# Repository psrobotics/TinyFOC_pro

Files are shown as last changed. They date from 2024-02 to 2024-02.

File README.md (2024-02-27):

# TinyFOC_pro

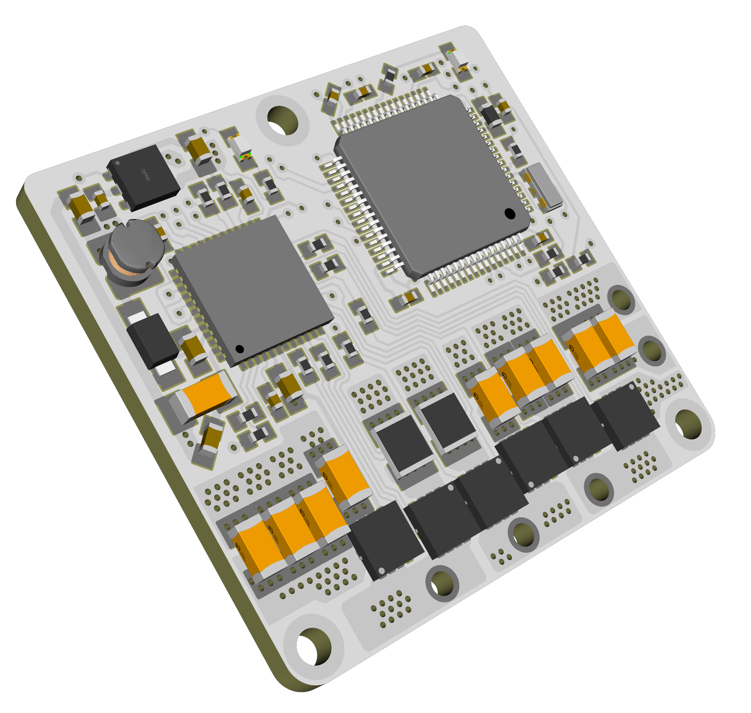
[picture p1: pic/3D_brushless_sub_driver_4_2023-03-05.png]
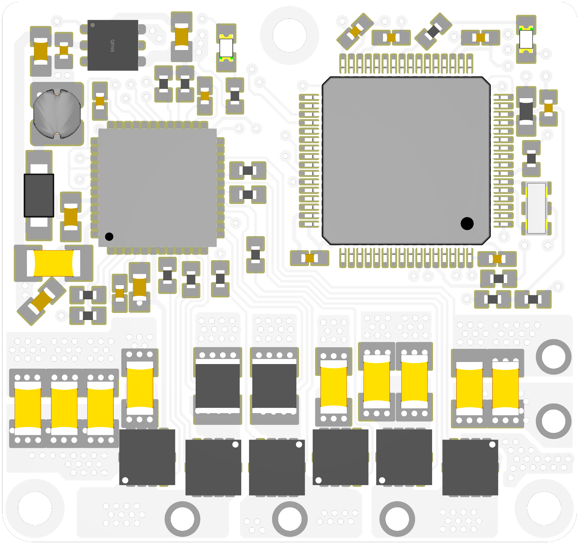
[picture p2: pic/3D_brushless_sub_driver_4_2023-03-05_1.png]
<br><br>
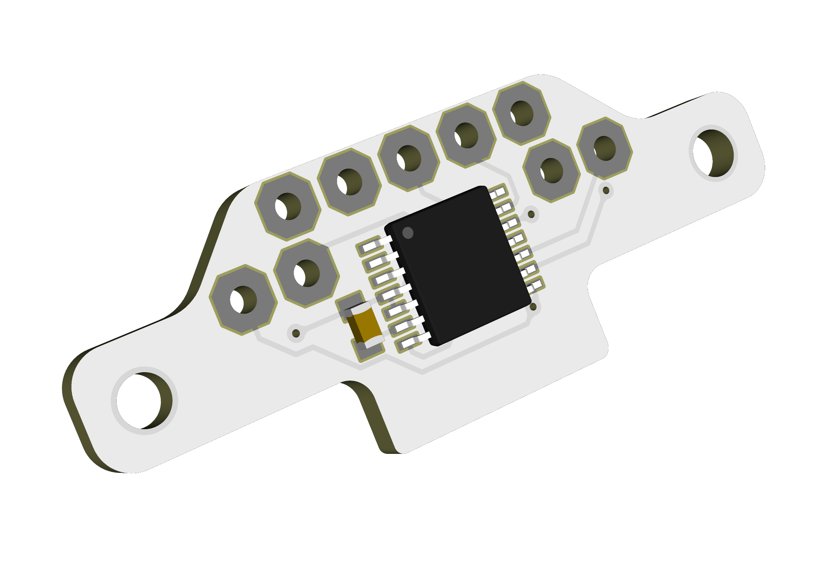
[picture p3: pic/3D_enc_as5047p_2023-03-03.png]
<br>
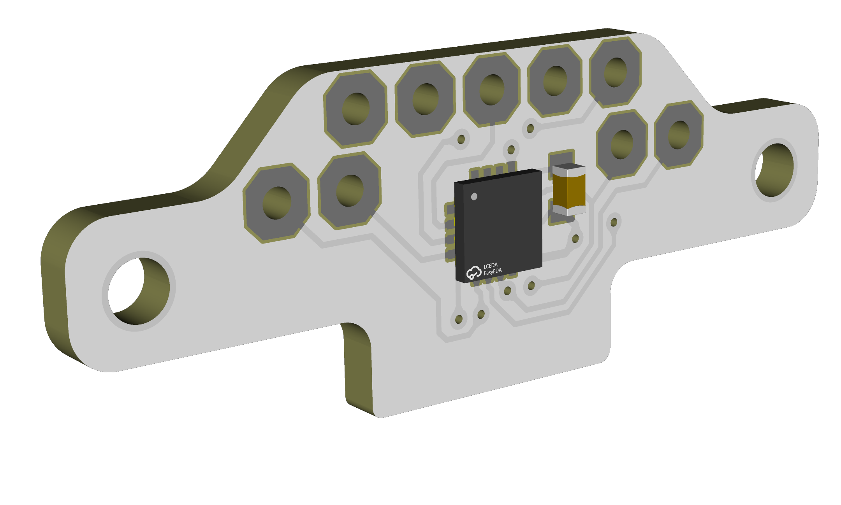
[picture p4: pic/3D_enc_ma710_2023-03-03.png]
<br>

<br><br>

* Compact brushless motor driver modified from [mit mini cheetah driver](https://github.com/bgkatz/3phase_integrated)
* 12 bit GMR-based encoder with MA710 or AS5047p
* CAN, hardware serial

Design file exported with [Autodesk EAGLE](https://www.autodesk.com/products/eagle/overview?term=1-YEAR&tab=subscription)

## License
MIT License

## Contact
* Shuang Peng, {shuangpe}@usc.edu

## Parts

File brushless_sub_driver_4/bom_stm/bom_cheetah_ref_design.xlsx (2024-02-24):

Supplied Parts
Qty Per Board | Value | Device | Package | Parts | MFG Part | 57
1 | DRV8323RH | DRV8323RH | QFN50P700X700X90-49N | U$1 | ‎DRV8323RSRGZT‎
2 | G | LED0603 | LED-0603 | LED1, LED2 | LTST-C191KRKT‎
1 | 3.3V 500 mA LDO | LDFM | DFN6-3X3 | LDFM33PUR | ‎LDFM33PUR‎
1 | MA700 | MA700 | QFN16 | U$11 | ‎MA700GQ-Z‎
1 | MCP2542 | MCP2542 | TDFN | U$6 | ‎MCP2542FDT-H/MNY‎
1 | SM07B-SRSS-TB | SM07B-SRSS-TB | SM07B-SRSS-TB | PROG | ‎SM07B-SRSS-TB(LF)(SN)‎
1 | STM32F446RET6 | STM32F446RET6 | TQFP64 | U$3 | ‎STM32F446RET6‎
6 | 60V | MOSFET | Power SO8 | Q1, Q2, Q3, Q4, Q5, Q6 | ‎TPH2R506PL,L1Q‎
9 | 10 uF 50v | C-USC1206K | C1206K | C1, C8, C11, C12, C13, C14, C15, C16, C17, C21, C22, C23, C24, C25, C26, C28, C29 | GRT31CR61H106ME01L
1 | 22uH 500 mA | SDR0302 | SDR0302 | L1 | ‎NRH3012T220MN‎
2 | 0.001 | R-US_R1210 | R1210 | R6, R7 | ‎PMR25HZPFV1L00‎
1 | 600r | INDUCTOR0603 | 603 | CHOKE | ‎PE-0603FB601ST‎
1 | 8 Mhz Ceramic Resonator | CSTCE | CSTCE | XT1 | ‎CSTNE8M00GH5L000R0‎
1 | 500 mA 60v | DIODE-SOD123 | SOD123 | D1 | ‎MBR0580S1-7‎
8 | .1 uF 10v X5R/X7R | C-USC0402K | C0402K | C18, C27, C31, C32, C33, C34, C41, VREFCAP | ‎CL05A104MP5NNNC
2 | .1 uF 50v X5R/X7R | C-USC0603K | C0603K | C2, C4 | ‎CC0603JRX7R9BB104‎
3 | 1 uF 10v X5R/X7R | C-USC0402K | C0402K | C7, C10, MC1 | ‎CL05A105MP5NNNC‎
1 | 1 uF 50v X5R/X7R | C-USC0603K | C0603K | C6 | ‎CL10A105KB8NNNC‎
4 | 10k 1% | R-US_R0402 | R0402 | R2, R3, R4 R27 | ‎RT0402DRE0710KL‎
1 | 150k 1% | R-US_R0402 | R0402 | R26 | ‎RMCF0402FT150K‎
2 | 200 5% | R-US_R0402 | R0402 | R5, R22 | ‎RC0402JR-07200RL‎
3 | 22 uF 10v X5R/X7R | C-USC0603K | C0603K | C3, C19, C20 | ‎CL10A226MPCNUBE‎
1 | 4.7 uF 10v X5R/X7R | C-USC0402K | C0402K | C9 | ‎GRM155R60J475ME87D‎
1 | 47 nF 50v X5R/X7R | C-USC0402K | C0402K | C5 | ‎CGA2B3X7R1H473M050BD‎
1 | 54.9k 1% | R-US_R0402 | R0402 | R1 | ‎RC0402FR-0754K9L‎
1 | 3-Pin |  | SM03B-SRSS-TB | SER1 | SM03B-SRSS-TB

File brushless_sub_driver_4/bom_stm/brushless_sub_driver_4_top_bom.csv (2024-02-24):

Comment | Designator | Footprint | LCSC Part #
.001 | R8 R9 | R1210
0.1uF | C2 C4 | C0603K
0.1uF | C17 | C1206K
1 uF | C6 | C0603K
1uF | C7 C10 | C0402K
1uF | C22 | C0402
2.2 | R6 R7 R10 R11 R12 R13 | R0402
3.3uH | CHOKE | 0603
4.7k | R14 R15 | R0402
4.7uF | C9 | C0402K
10k | R2 R3 R4 R27 | R0402
10uF | C1 C8 C11 C12 C13 C14 C15 C16 C18 | C1206K
22 uF | C3 | C0603K
22uF | C25 | C0603K
22uH | L1 | SDR0302
47 nF | C5 | C0402K
54.9k | R1 | R0402
100nF | C27 C31 C32 | C0402K
100nF | C41 | C0402
100nF | VREFCAP | C0402K
150k | R26 | R0402
200 | R5 R22 | R0402
AON7544 | Q7 Q8 Q9 Q10 Q11 Q12 | AON7544
CSTCE | XT1 | CSTCE
DRV8323RH | DRV1 | QFN50P700X700X90-49N
LD39050PUR | U3 | SON95P300X300X100-7N
SOD123 | D1 | SOD123
STM32F446RET6 | U1 | TQFP64
green | D2 D3 | 0603P

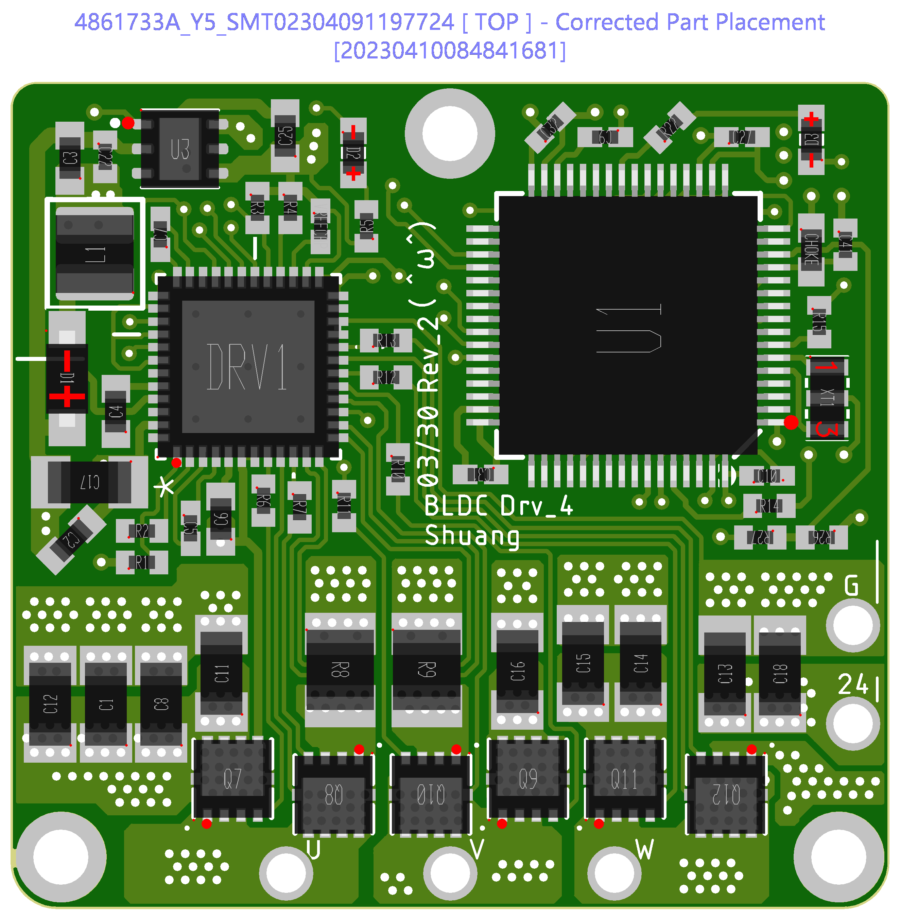
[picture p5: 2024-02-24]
brushless_sub_driver_4/bom_stm/Produce_SMT_FINAL_Snapshot_top_0410.png

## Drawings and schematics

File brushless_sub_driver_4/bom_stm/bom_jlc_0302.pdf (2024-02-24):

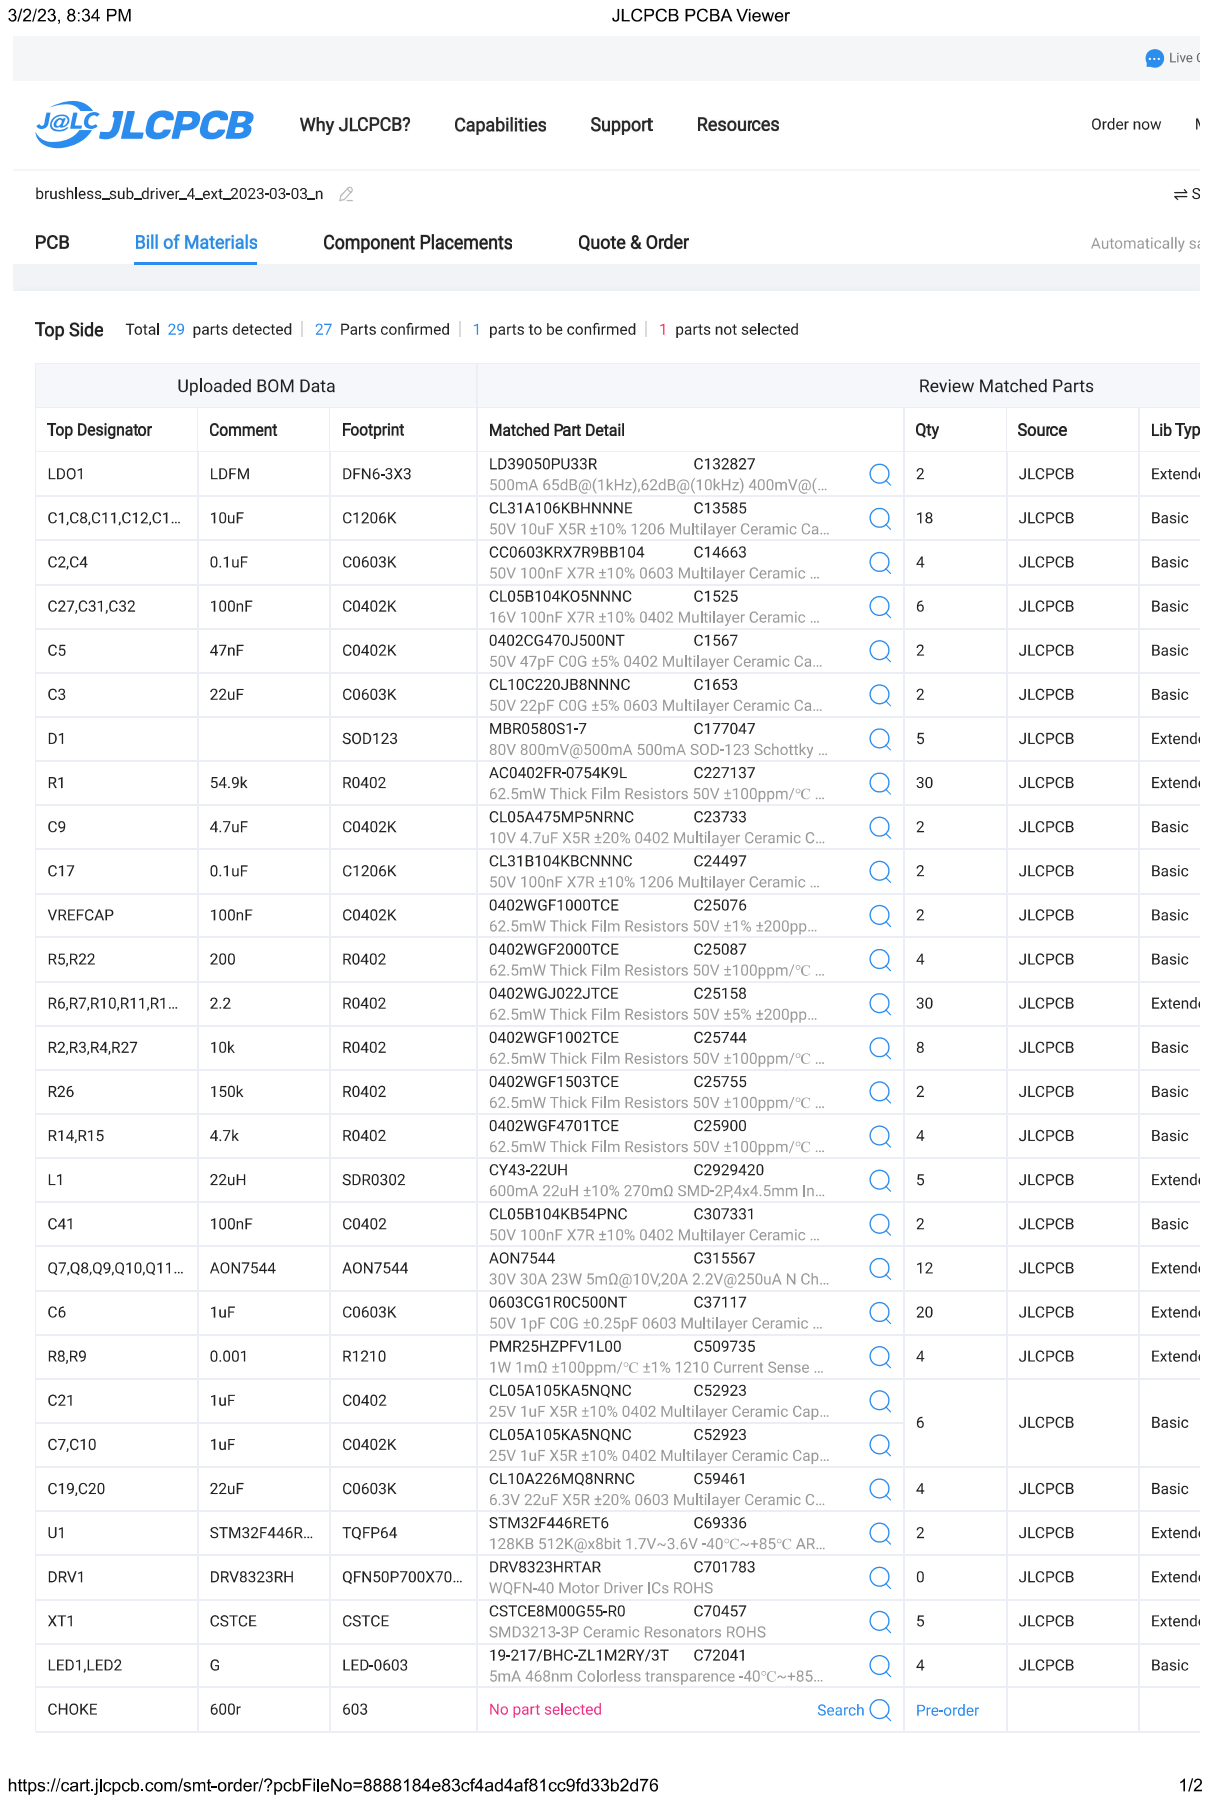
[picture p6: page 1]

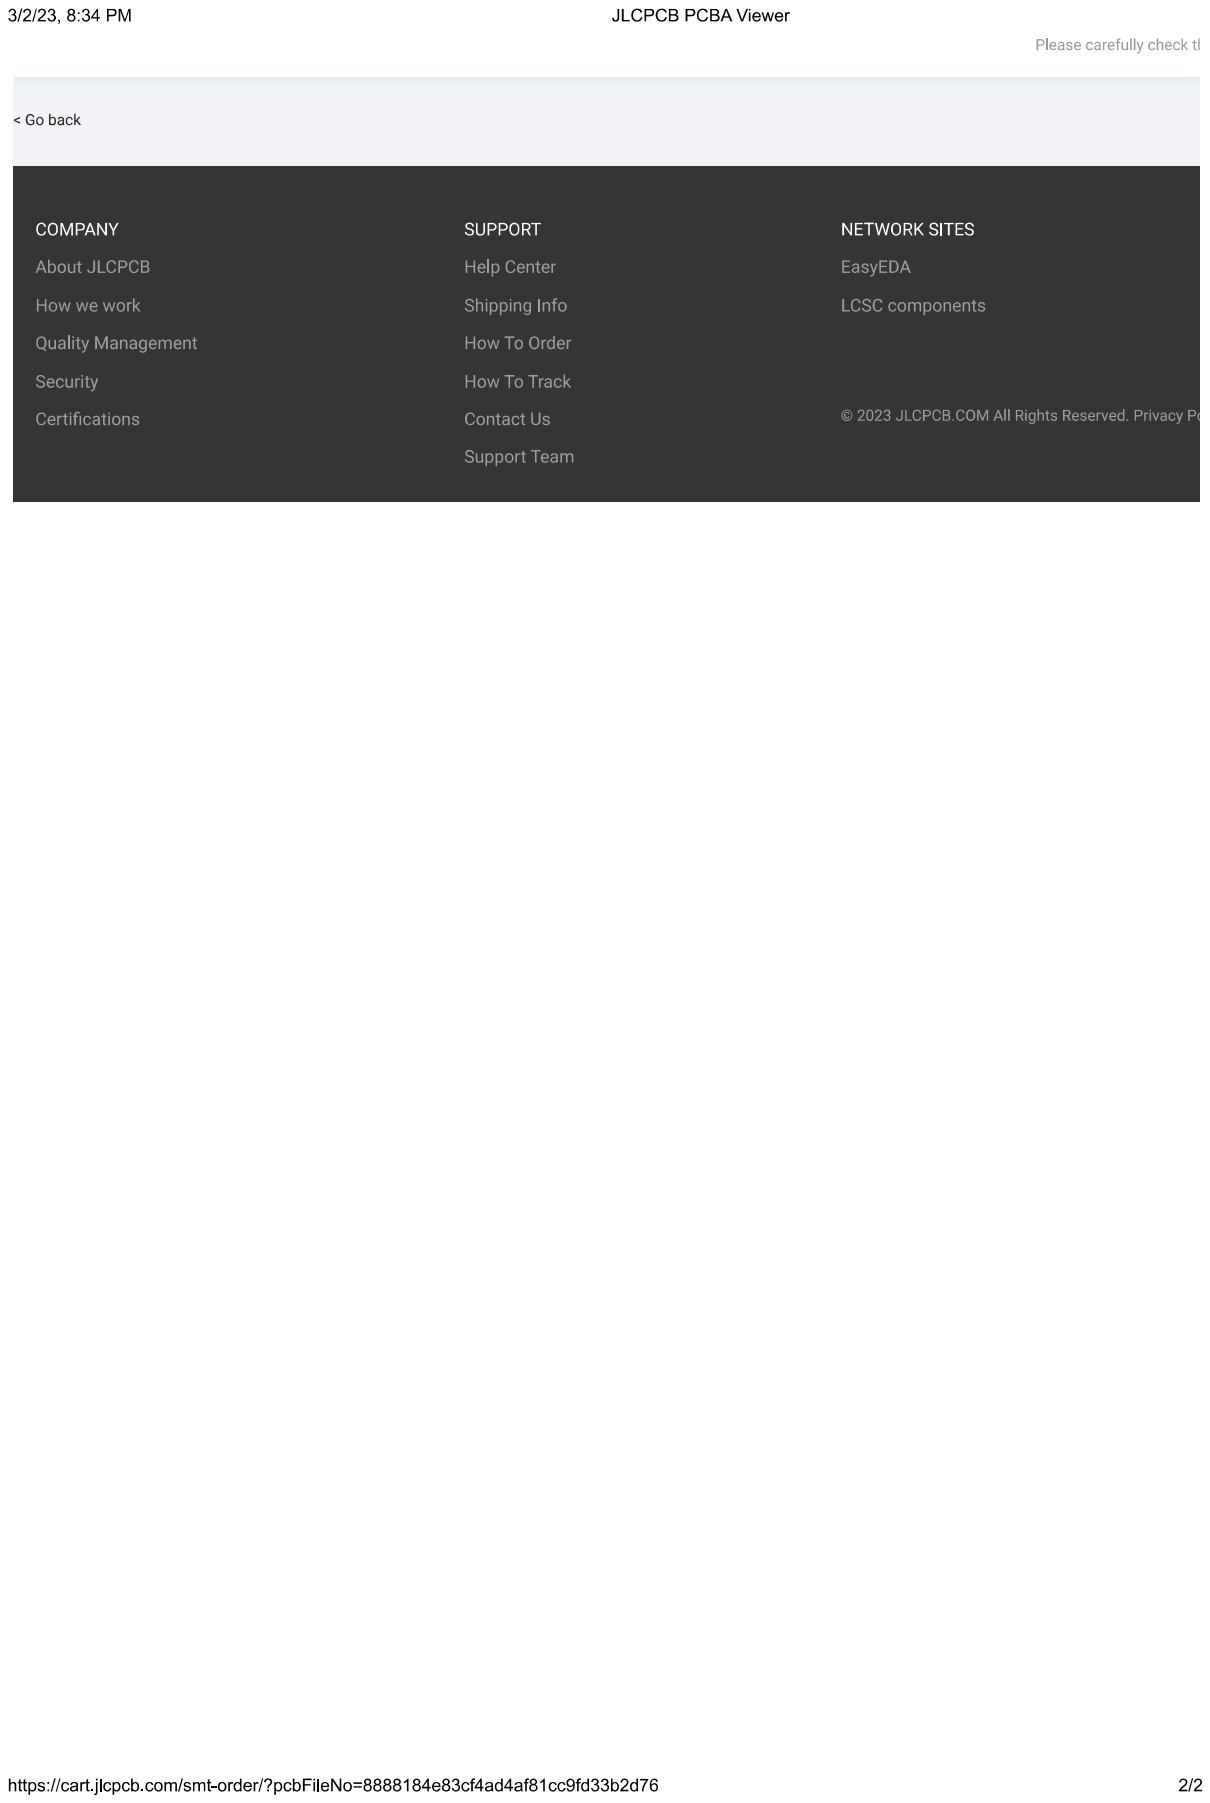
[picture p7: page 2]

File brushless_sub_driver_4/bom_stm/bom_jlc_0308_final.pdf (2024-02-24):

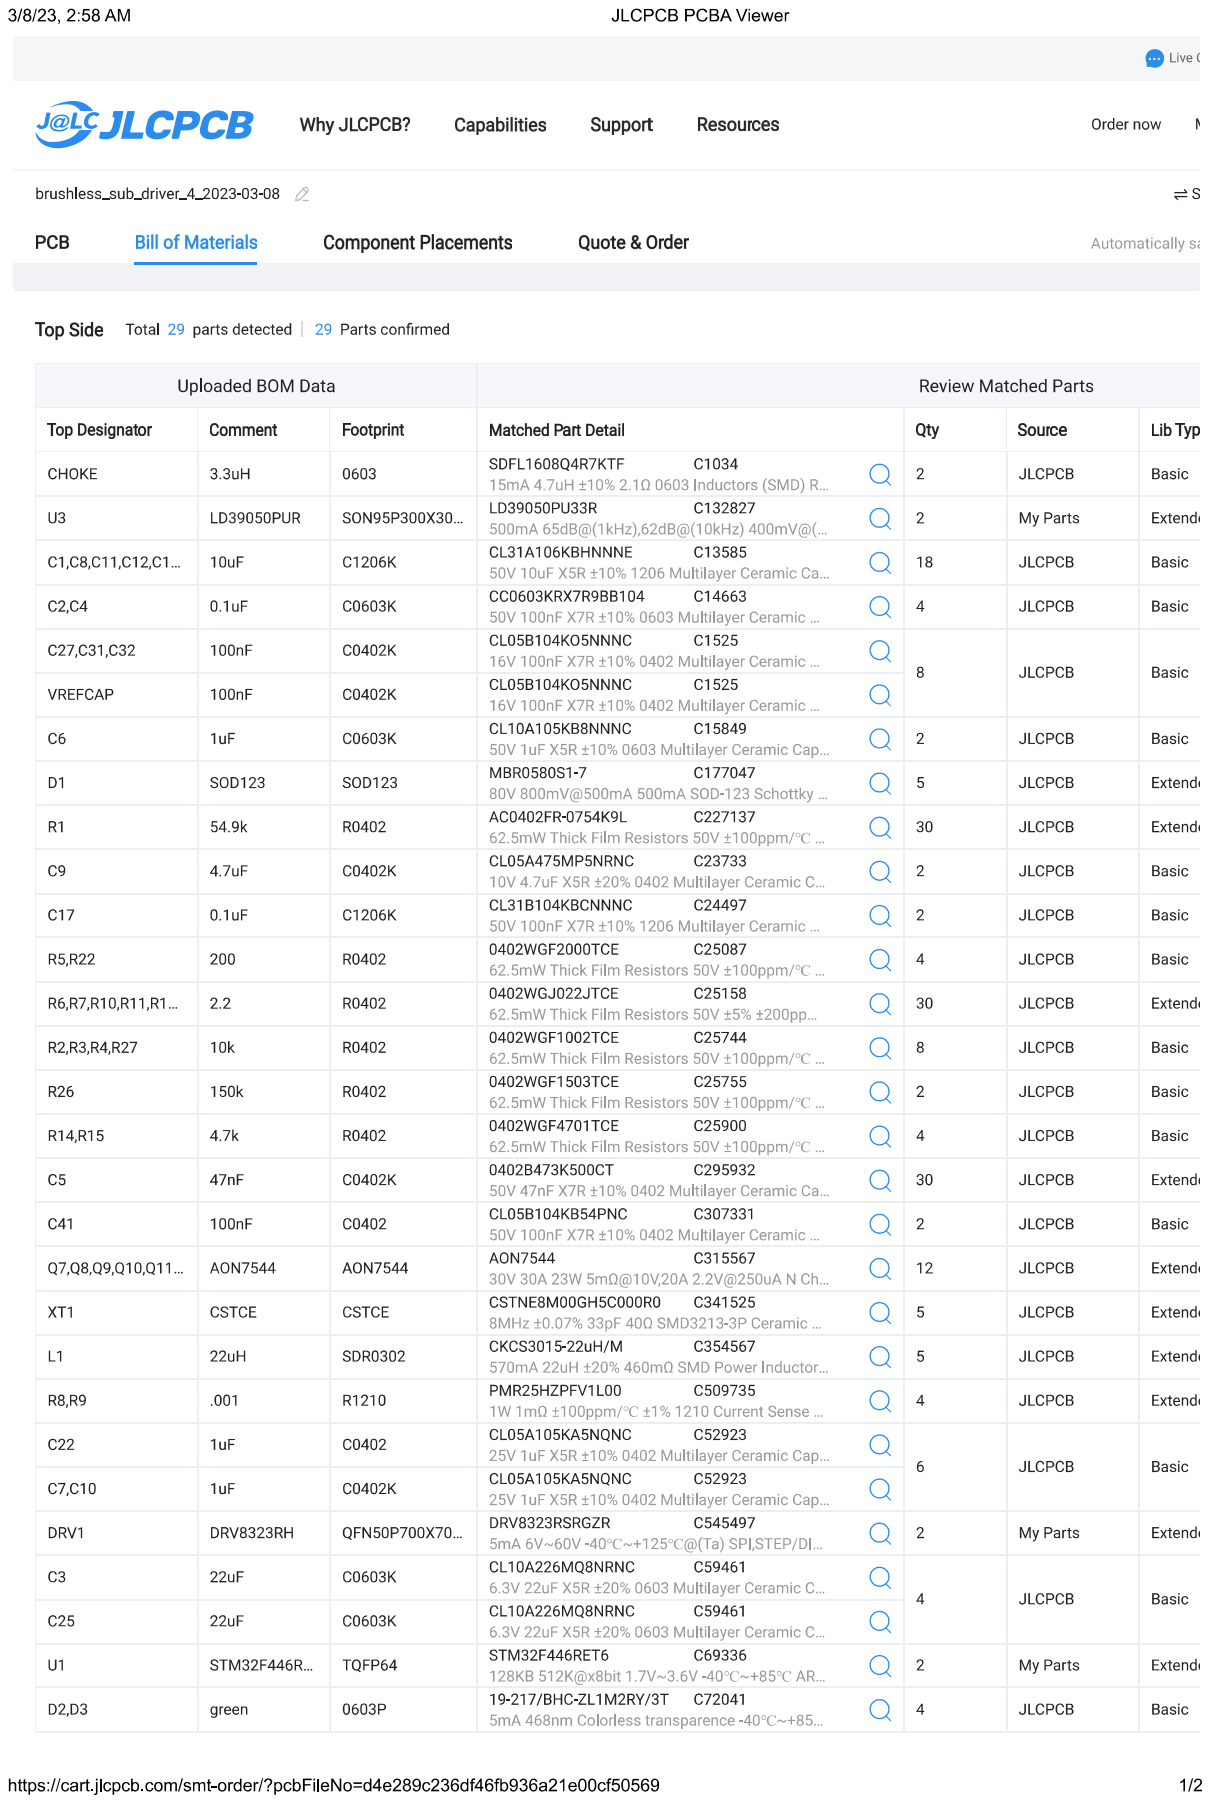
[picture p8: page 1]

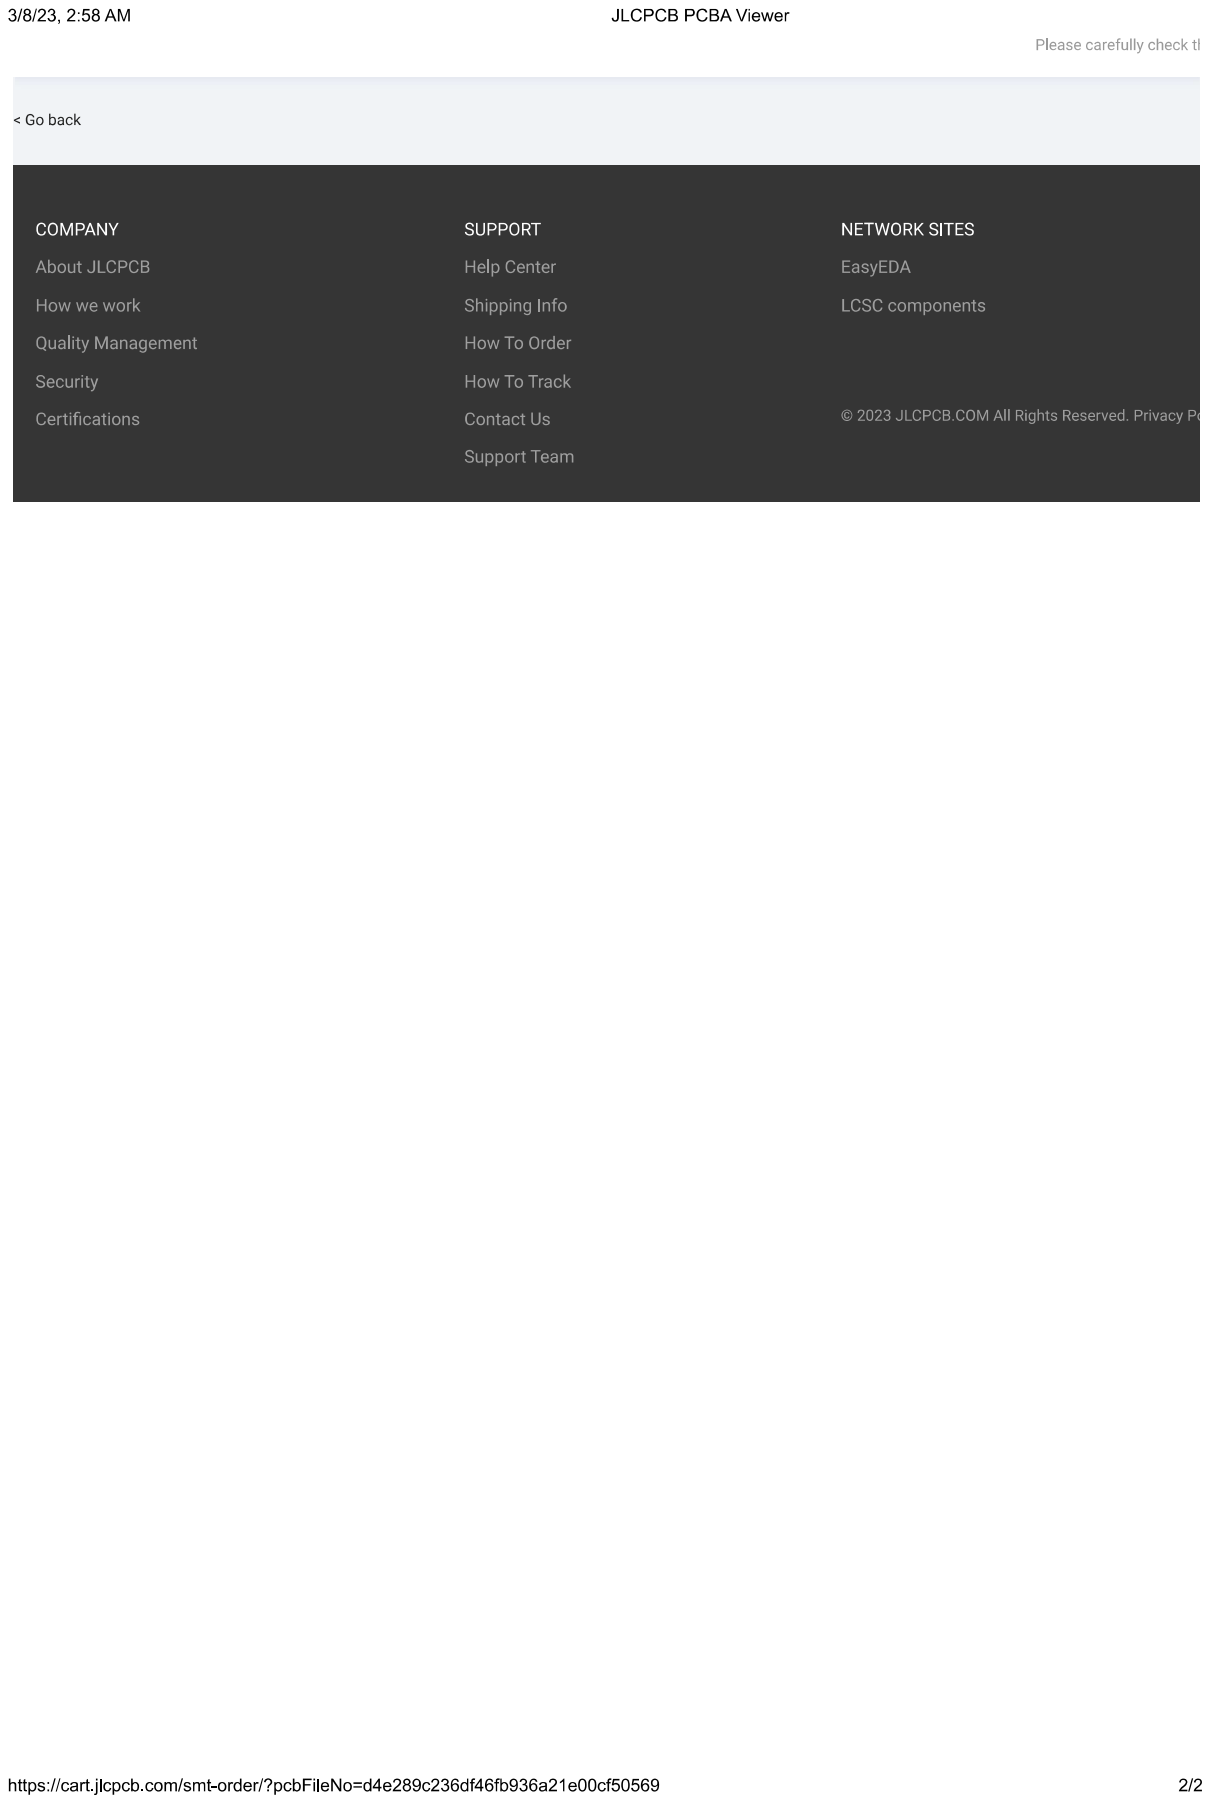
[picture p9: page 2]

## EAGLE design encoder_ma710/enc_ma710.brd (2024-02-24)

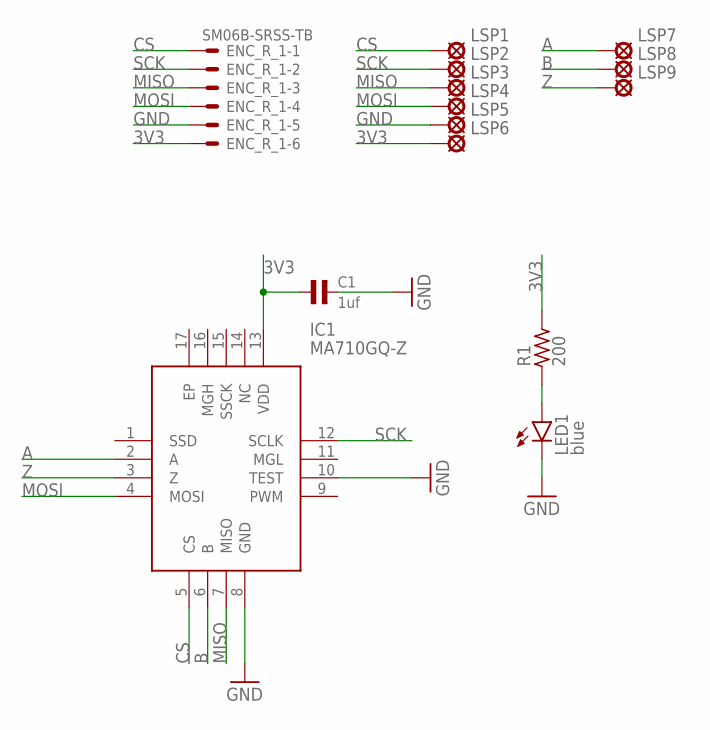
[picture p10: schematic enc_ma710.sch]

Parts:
C1: 1uf; 0603
ENC_R_1: SM06B-SRSS-TB
IC1: MA710GQ-Z; QFN50P300X300X100-17N
LED1: blue; SML0603
LSP1, LSP2, LSP3, LSP4, LSP5, LSP6, LSP7, LSP8, LSP9: LSP10
R1: 200; R0603

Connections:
3V3: C1.1, ENC_R_1.6, IC1.13 (VDD), LSP6.MP, R1.2
A: IC1.2 (A), LSP7.MP
B: IC1.6 (B), LSP8.MP
CS: ENC_R_1.1, IC1.5 (CS), LSP1.MP
GND: C1.2, ENC_R_1.5, IC1.8 (GND), IC1.10 (TEST), LED1.C, LSP5.MP
MISO: ENC_R_1.3, IC1.7 (MISO), LSP3.MP
MOSI: ENC_R_1.4, IC1.4 (MOSI), LSP4.MP
unnamed: LED1.A, R1.1
SCK: ENC_R_1.2, IC1.12 (SCLK), LSP2.MP
Z: IC1.3 (Z), LSP9.MP

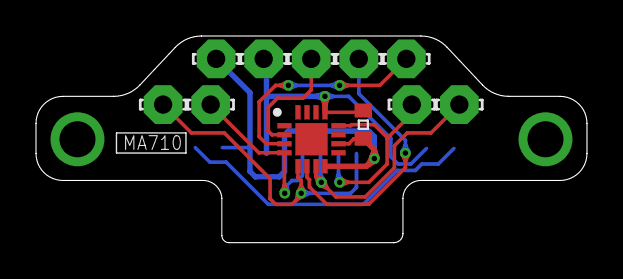
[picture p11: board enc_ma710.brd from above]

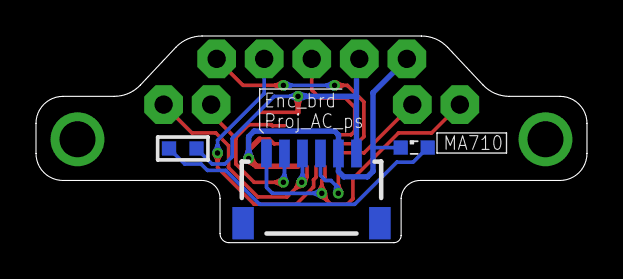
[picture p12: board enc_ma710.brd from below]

Board: 2 copper layers, 30.6 x 11.5 mm, 14 parts (3 on the bottom side), 10 nets.

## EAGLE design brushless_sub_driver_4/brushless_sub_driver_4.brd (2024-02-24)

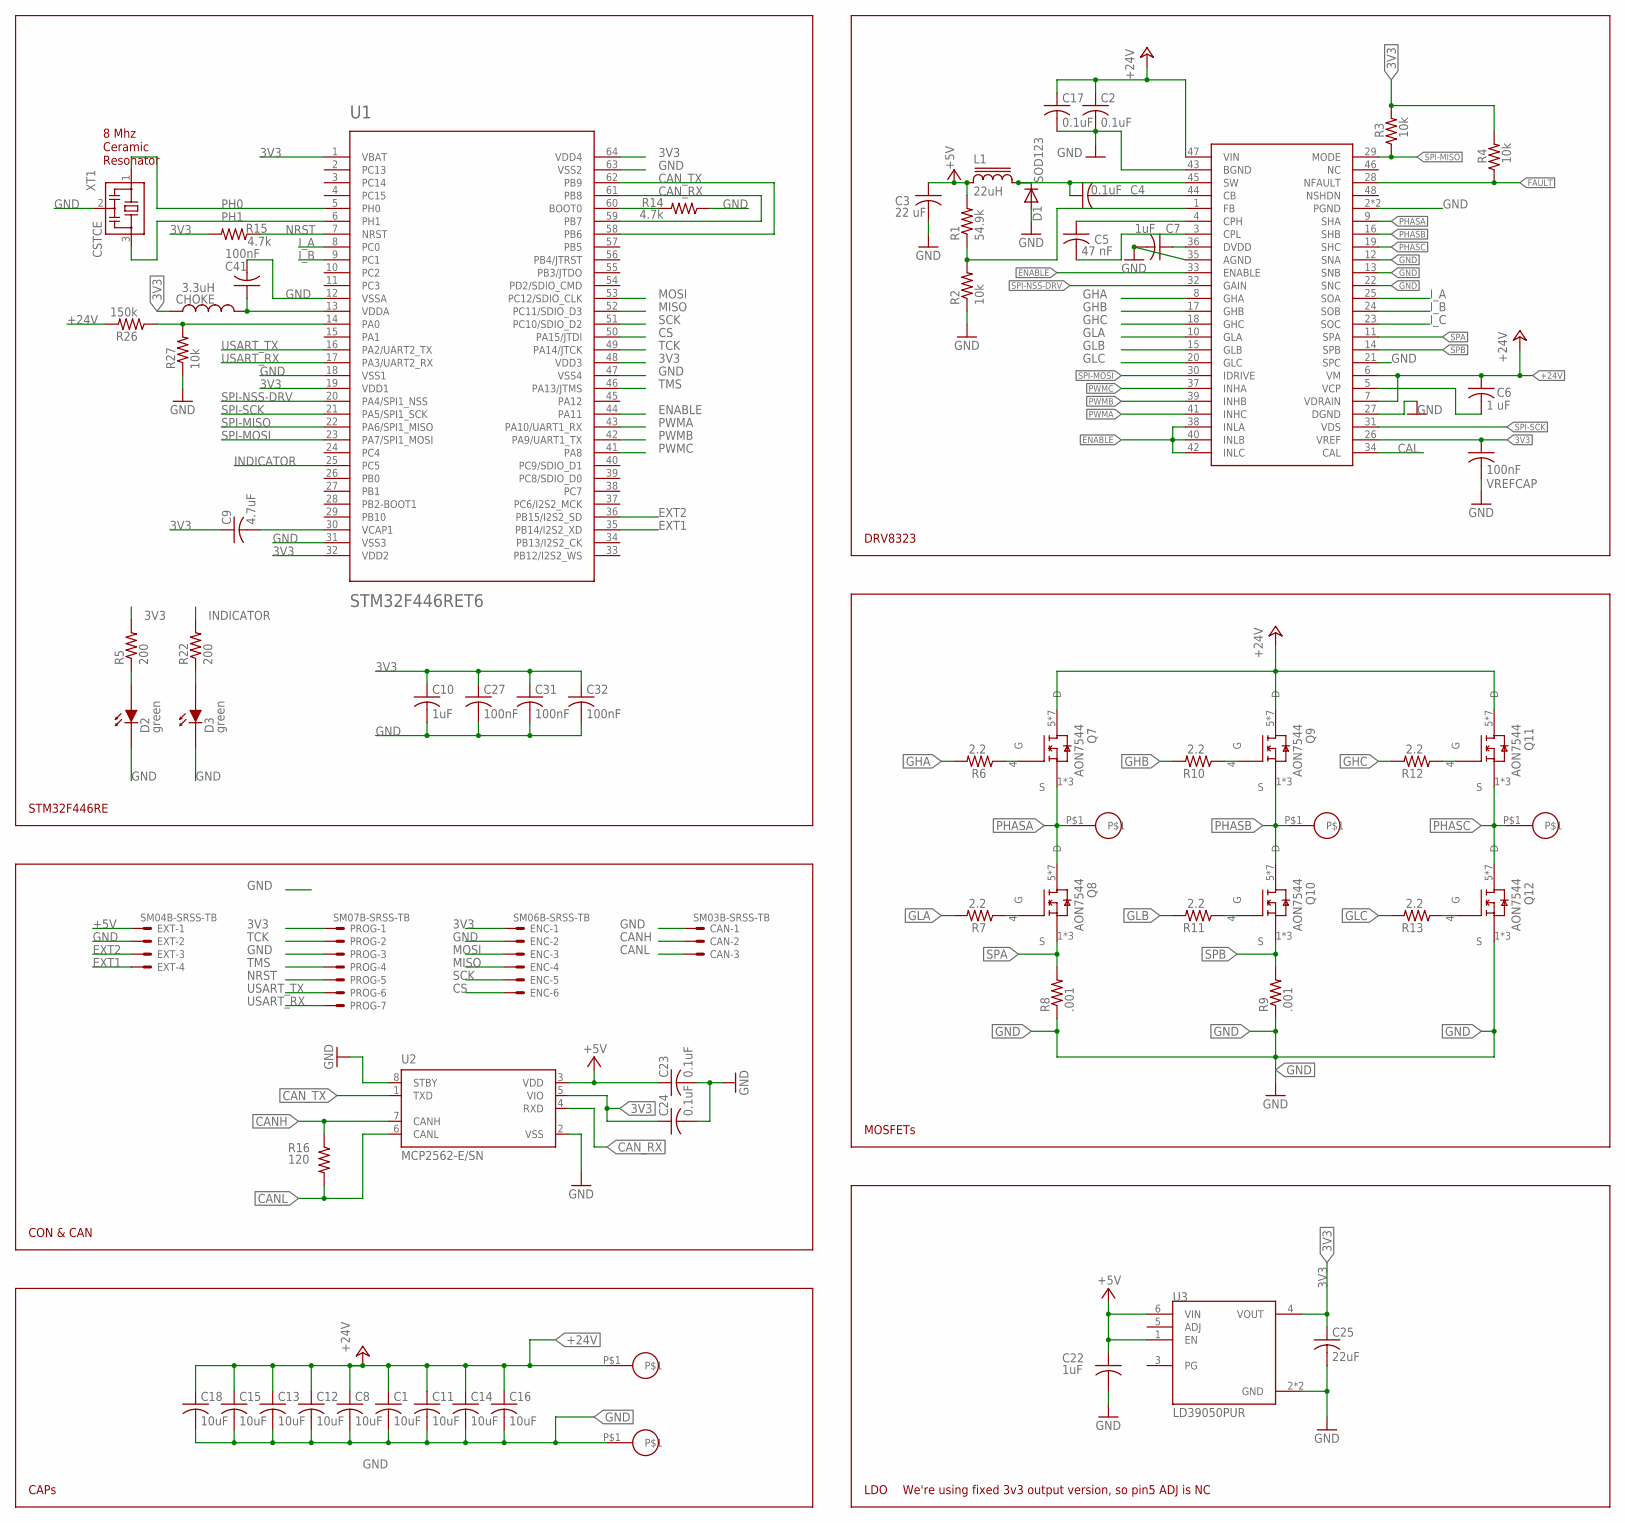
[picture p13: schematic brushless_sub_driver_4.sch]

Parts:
C1, C8, C11, C12, C13, C14, C15, C16, C18: 10uF; C1206K
C2, C4, C23, C24: 0.1uF; C0603K
C3: 22 uF; C0603K
C5: 47 nF; C0402K
C6: 1 uF; C0603K
C7, C10: 1uF; C0402K
C9: 4.7uF; C0402K
C17: 0.1uF; C1206K
C22: 1uF; C0402
C25: 22uF; C0603K
C27, C31, C32: 100nF; C0402K
C41: 100nF; C0402
CAN: SM03B-SRSS-TB
CHOKE: 3.3uH; 0603
D1: SOD123
D2, D3: green; 0603P
DRV1: DRV8323RH; QFN50P700X700X90-49N
ENC: SM06B-SRSS-TB
EXT: SM04B-SRSS-TB
L1: 22uH; SDR0302
O_A: 18_AWG_PAD
O_B: 18_AWG_PAD
O_C: 18_AWG_PAD
PROG: SM07B-SRSS-TB
Q7, Q8, Q9, Q10, Q11, Q12: AON7544
R1: 54.9k; R0402
R2, R3, R4, R27: 10k; R0402
R5, R22: 200; R0402
R6, R7, R10, R11, R12, R13: 2.2; R0402
R8, R9: .001; R1210
R14, R15: 4.7k; R0402
R16: 120; R0603
R26: 150k; R0402
U1: STM32F446RET6; TQFP64
U2: MCP2562-E/SN; SOIC127P600X175-8N
U3: LD39050PUR; SON95P300X300X100-7N
U$8, U$10: 18_AWG_PAD
VREFCAP: 100nF; C0402K
XT1: CSTCE

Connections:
3V3: C9.1, C10.1, C24.1, C25.1, C27.1, C31.1, C32.1, CHOKE.1, DRV1.26 (VREF), ENC.1, PROG.1, R3.2, R4.2, R5.2, R15.2, U1.1 (VBAT), U1.19 (VDD1), U1.32 (VDD2), U1.48 (VDD3), U1.64 (VDD4), U2.5 (VIO), U3.4 (VOUT), VREFCAP.1
+5V: C3.1, C22.1, C23.1, EXT.1, L1.1, R1.2, U2.3 (VDD), U3.1 (EN), U3.6 (VIN)
+24V: C1.1, C2.1, C6.1, C8.1, C11.1, C12.1, C13.1, C14.1, C15.1, C16.1, C17.1, C18.1, DRV1.6 (VM), DRV1.7 (VDRAIN), DRV1.47 (VIN), Q7.5 (D), Q7.6 (D), Q7.7 (D), Q7.8 (D), Q7.9 (D), Q7.10 (D), Q7.11 (D), Q9.5 (D), Q9.6 (D), Q9.7 (D), Q9.8 (D), Q9.9 (D), Q9.10 (D), Q9.11 (D), Q11.5 (D), Q11.6 (D), Q11.7 (D), Q11.8 (D), Q11.9 (D), Q11.10 (D), Q11.11 (D), R26.2, U$8.P$1
BOOT: C4.2, DRV1.44 (CB)
CAL: DRV1.34 (CAL)
CANH: CAN.2, R16.1, U2.7 (CANH)
CANL: CAN.3, R16.2, U2.6 (CANL)
CAN_RX: U1.59 (PB7), U1.61 (PB8), U2.4 (RXD)
CAN_TX: U1.58 (PB6), U1.62 (PB9), U2.1 (TXD)
CPH: C5.1, DRV1.4 (CPH)
CPL: C5.2, DRV1.3 (CPL)
CS: ENC.6, U1.50 (PA15/JTDI)
DEVICE3.3: C7.1, DRV1.36 (DVDD)
ENABLE: DRV1.33 (ENABLE), DRV1.38 (INLA), DRV1.40 (INLB), DRV1.42 (INLC), U1.44 (PA11)
EXT1: EXT.4, U1.35 (PB14/I2S2_XD)
EXT2: EXT.3, U1.36 (PB15/I2S2_SD)
FAULT: DRV1.28 (NFAULT), R4.1
FB: DRV1.1 (FB), R1.1, R2.2
GHA: DRV1.8 (GHA), R6.2
GHB: DRV1.17 (GHB), R10.2
GHC: DRV1.18 (GHC), R12.2
GLA: DRV1.10 (GLA), R7.2
GLB: DRV1.15 (GLB), R11.2
GLC: DRV1.20 (GLC), R13.2
GND: C1.2, C2.2, C3.2, C7.2, C8.2, C10.2, C11.2, C12.2, C13.2, C14.2, C15.2, C16.2, C17.2, C18.2, C22.2, C23.2, C24.2, C25.2, C27.2, C31.2, C32.2, C41.2, CAN.1, D1.A, D2.2 (D_OUT), D3.2 (D_OUT), DRV1.2 (PGND), DRV1.12 (SNA), DRV1.13 (SNB), DRV1.21 (SPC), DRV1.22 (SNC), DRV1.27 (DGND), DRV1.35 (AGND), DRV1.43 (BGND), DRV1.49 (PGND), ENC.2, EXT.2, PROG.3, Q12.1 (S), Q12.2 (S), Q12.3 (S), R2.1, R8.1, R9.1, R14.1, R27.1, U1.12 (VSSA), U1.18 (VSS1), U1.31 (VSS3), U1.47 (VSS4), U1.63 (VSS2), U2.2 (VSS), U2.8 (STBY), U3.2 (GND), U3.7 (GND), U$10.P$1, VREFCAP.2, XT1.2
INDICATOR: R22.2, U1.25 (PC5)
I_A: DRV1.25 (SOA), U1.8 (PC0)
I_B: DRV1.24 (SOB), U1.9 (PC1)
I_C: DRV1.23 (SOC)
MISO: ENC.4, U1.52 (PC11/SDIO_D3)
MOSI: ENC.3, U1.53 (PC12/SDIO_CLK)
unnamed: D2.1 (D_IN), R5.1
unnamed: C41.1, CHOKE.2, U1.13 (VDDA)
unnamed: C9.2, U1.30 (VCAP1)
unnamed: Q7.4 (G), R6.1
unnamed: Q8.4 (G), R7.1
unnamed: Q9.4 (G), R10.1
unnamed: Q10.4 (G), R11.1
unnamed: Q11.4 (G), R12.1
unnamed: Q12.4 (G), R13.1
unnamed: R14.2, U1.60 (BOOT0)
unnamed: R26.1, R27.2, U1.14 (PA0)
unnamed: D3.1 (D_IN), R22.1
NRST: PROG.5, R15.1, U1.7 (NRST)
PH0: U1.5 (PH0), XT1.1
PH1: U1.6 (PH1), XT1.3
PHASA: DRV1.9 (SHA), O_A.P$1, Q7.1 (S), Q7.2 (S), Q7.3 (S), Q8.5 (D), Q8.6 (D), Q8.7 (D), Q8.8 (D), Q8.9 (D), Q8.10 (D), Q8.11 (D)
PHASB: DRV1.16 (SHB), O_B.P$1, Q9.1 (S), Q9.2 (S), Q9.3 (S), Q10.5 (D), Q10.6 (D), Q10.7 (D), Q10.8 (D), Q10.9 (D), Q10.10 (D), Q10.11 (D)
PHASC: DRV1.19 (SHC), O_C.P$1, Q11.1 (S), Q11.2 (S), Q11.3 (S), Q12.5 (D), Q12.6 (D), Q12.7 (D), Q12.8 (D), Q12.9 (D), Q12.10 (D), Q12.11 (D)
PWMA: DRV1.41 (INHC), U1.43 (PA10/UART1_RX)
PWMB: DRV1.39 (INHB), U1.42 (PA9/UART1_TX)
PWMC: DRV1.37 (INHA), U1.41 (PA8)
SCK: ENC.5, U1.51 (PC10/SDIO_D2)
SPA: DRV1.11 (SPA), Q8.1 (S), Q8.2 (S), Q8.3 (S), R8.2
SPB: DRV1.14 (SPB), Q10.1 (S), Q10.2 (S), Q10.3 (S), R9.2
SPI-MISO: DRV1.29 (MODE), R3.1, U1.22 (PA6/SPI1_MISO)
SPI-MOSI: DRV1.30 (IDRIVE), U1.23 (PA7/SPI1_MOSI)
SPI-NSS-DRV: DRV1.32 (GAIN), U1.20 (PA4/SPI1_NSS)
SPI-SCK: DRV1.31 (VDS), U1.21 (PA5/SPI1_SCK)
SW: C4.1, D1.C, DRV1.45 (SW), L1.2
TCK: PROG.2, U1.49 (PA14/JTCK)
TMS: PROG.4, U1.46 (PA13/JTMS)
USART_RX: PROG.7, U1.17 (PA3/UART2_RX)
USART_TX: PROG.6, U1.16 (PA2/UART2_TX)
VCP: C6.2, DRV1.5 (VCP)

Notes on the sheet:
STM32F446RE
DRV8323
MOSFETs
LDO
CAPs
CON & CAN
8 Mhz Ceramic Resonator
We're using fixed 3v3 output version, so pin5 ADJ is NC

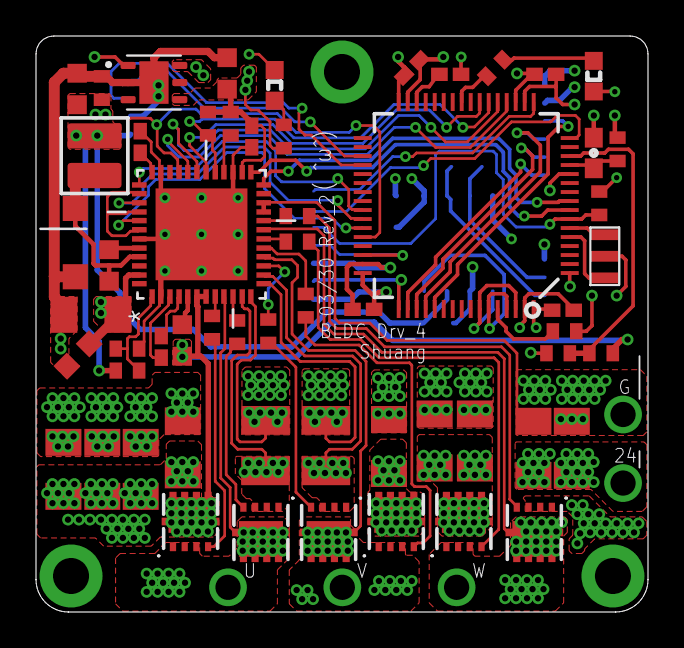
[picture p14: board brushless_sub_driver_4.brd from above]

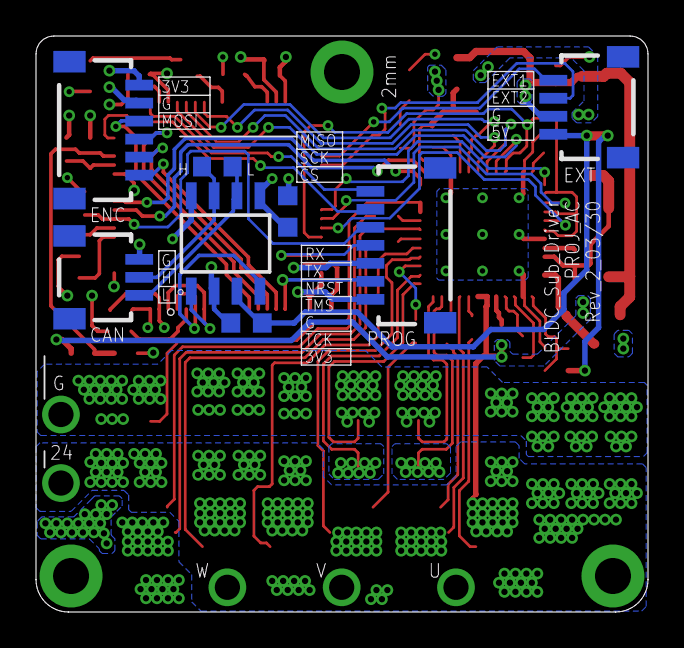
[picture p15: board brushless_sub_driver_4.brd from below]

Board: 4 copper layers, 34.0 x 32.0 mm, 71 parts (8 on the bottom side), 63 nets.

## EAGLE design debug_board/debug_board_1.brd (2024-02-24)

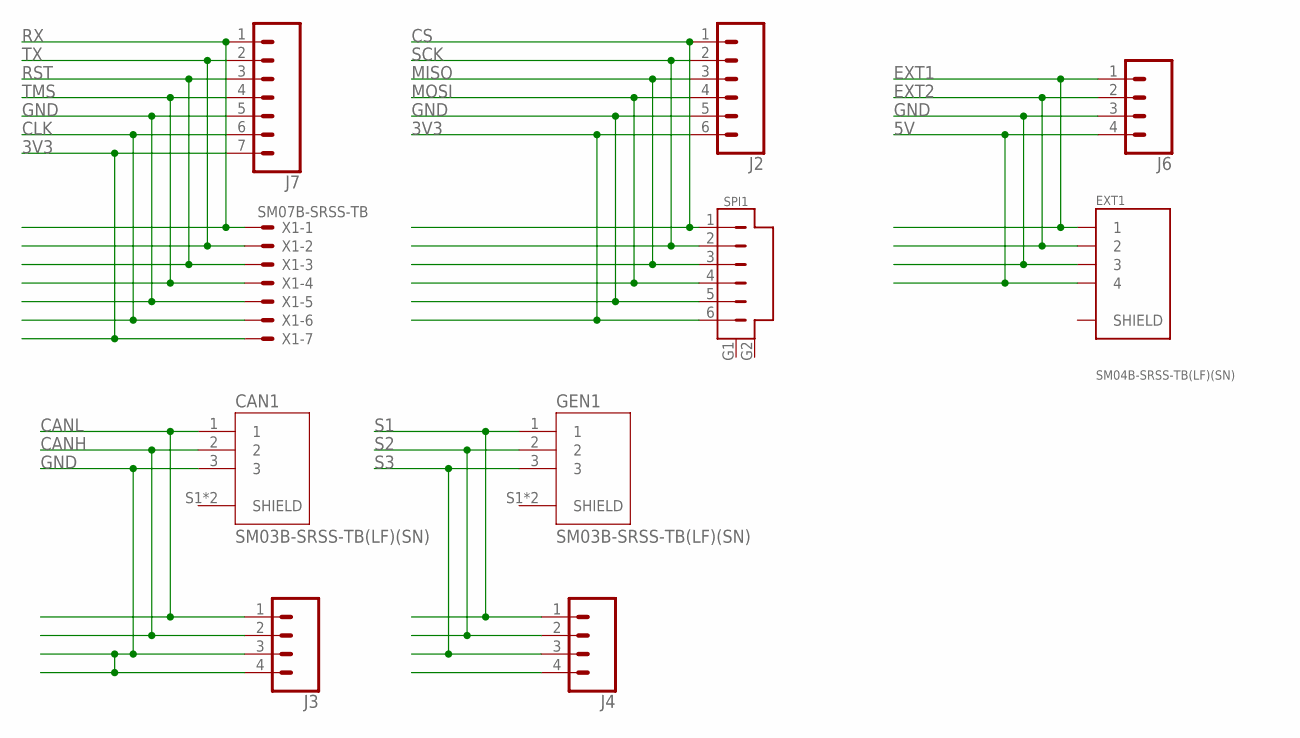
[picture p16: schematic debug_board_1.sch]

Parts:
CAN1: SM03B-SRSS-TB(LF)(SN); JST_SM03B-SRSS-TB(LF)(SN)
EXT1: SM04B-SRSS-TB(LF)(SN); JST_SM04B-SRSS-TB(LF)(SN)
GEN1: SM03B-SRSS-TB(LF)(SN); JST_SM03B-SRSS-TB(LF)(SN)
J2: CONN_06LONGPADS; 1X06_LONGPADS
J3, J4, J6: CONN_04LONGPADS; 1X04_LONGPADS
J7: CONN_07LONGPADS; 1X07_LONGPADS
SPI1: SM06B-SRSS-TB; SM06B
X1: SM07B-SRSS-TB

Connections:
3V3: J2.6, J7.7, SPI1.6, X1.7
5V: EXT1.4, J6.4
CANH: CAN1.2, J3.2
CANL: CAN1.1, J3.1
CLK: J7.6, X1.6
CS: J2.1, SPI1.1
EXT1: EXT1.1, J6.1
EXT2: EXT1.2, J6.2
GND: CAN1.3, EXT1.3, J2.5, J3.3, J3.4, J6.3, J7.5, SPI1.5, X1.5
MISO: J2.3, SPI1.3
MOSI: J2.4, SPI1.4
RST: J7.3, X1.3
RX: J7.1, X1.1
S1: GEN1.1, J4.1
S2: GEN1.2, J4.2
S3: GEN1.3, J4.3
SCK: J2.2, SPI1.2
TMS: J7.4, X1.4
TX: J7.2, X1.2

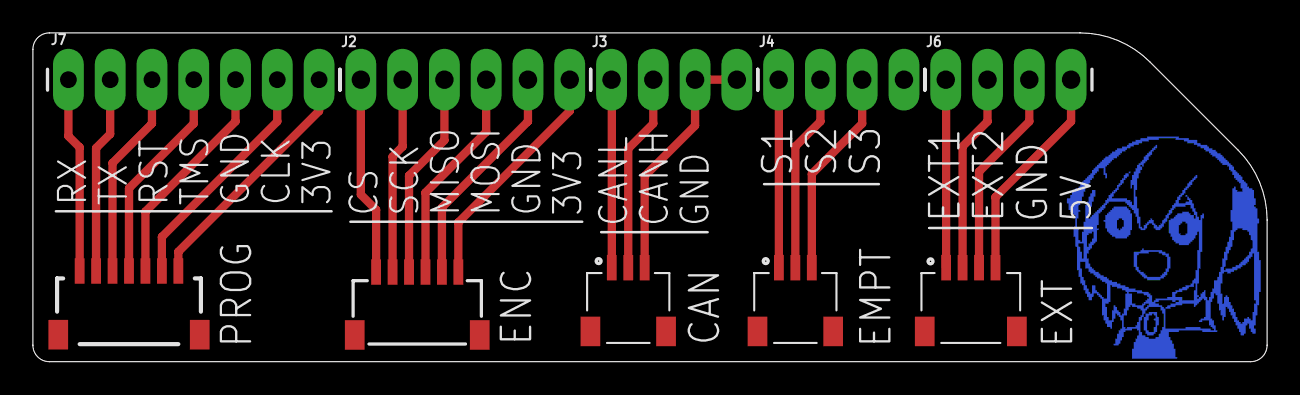
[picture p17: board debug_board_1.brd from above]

Board: 2 copper layers, 75.0 x 20.0 mm, 11 parts (0 on the bottom side), 19 nets.

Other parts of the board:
U$1: SODAYO_1

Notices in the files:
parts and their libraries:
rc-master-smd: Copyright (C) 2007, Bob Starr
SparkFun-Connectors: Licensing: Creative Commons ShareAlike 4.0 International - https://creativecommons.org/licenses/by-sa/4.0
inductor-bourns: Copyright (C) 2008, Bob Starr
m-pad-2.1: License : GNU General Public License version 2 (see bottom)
